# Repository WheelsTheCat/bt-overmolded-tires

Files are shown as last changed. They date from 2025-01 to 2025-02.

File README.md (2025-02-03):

# Box Turtle Overmolded Tires
# Thank you to Transmutated in the Box Turtle Discord for the excellent writeup and pictures!

Discussion here: [Discord Box Turtle Discussion](https://discord.com/channels/1229586267671629945/1315355814512562242 "Discord Box Turtle discussion").

## Tools
* hot glue gun
* hobby knife
* small pliers
* diagonal cutting pliers or something else strong enough to cut the "ice-cube tray"
* fine-tipped screwdriver or similar prying device

## Materials
* two-part rubber silicone; 10a, 15a and 20a will work.

## STL Files To Print
You can print these in whatever sacrificial filament you want to use as most of these parts won't be reusable. 
## The exception is the new-style wheels. Print these in whatever filament you are printing all of your accent color parts in to match your box turtle build.

Print settings:
- 0.2mm layer height.
- The Spiral Insert should be printed in vase mode and using the arachne wall generator. 
(Quality, Wall Generator, Arachne). Thanks Robnex!

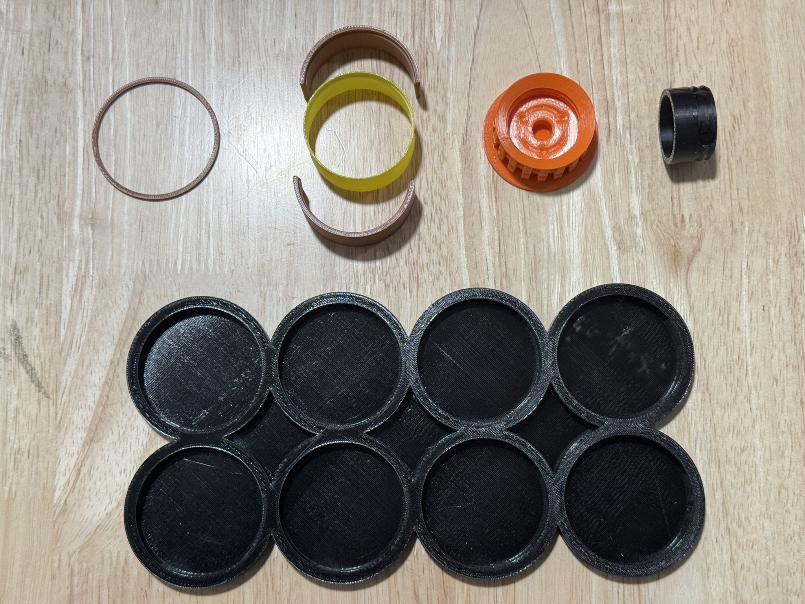
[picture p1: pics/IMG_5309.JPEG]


* 1 x [Ice Cube Tray](https://github.com/WheelsTheCat/bt-overmolded-tires/blob/main/stls/Ice%20Cube%20Tray.stl) - second row, position 1 in black
* 8 x [Retainers](https://github.com/WheelsTheCat/bt-overmolded-tires/blob/main/stls/Retainer.stl) - first row, position 1 in brown
* 8 x [Part 1](https://github.com/WheelsTheCat/bt-overmolded-tires/blob/main/stls/Part%201.stl) - first row, position 2, above yellow spiral insert
* 8 x [Part 2](https://github.com/WheelsTheCat/bt-overmolded-tires/blob/main/stls/Part%202.stl) - first row, position 2, below yellow spiral insert
* 8 x [Spiral Inserts](https://github.com/WheelsTheCat/bt-overmolded-tires/blob/main/stls/Spiral%20Insert.stl) first row, position two, in yellow
* 8 x [New Style Wheels](https://github.com/WheelsTheCat/bt-overmolded-tires/blob/main/stls/New%20Style%20Wheel.stl) first row, position 3, in orange
* 8 x [New Style Wheel Plugs](https://github.com/WheelsTheCat/bt-overmolded-tires/blob/main/stls/New%20Style%20Wheel%20Plug.stl) first row, position 4, in black

## Step 1
Assemble the spiral inserts combined with the retainer and parts 1 & 2. Observe that there is a lip that must be aligned for both parts and the spiral inserts. Once assembled, slide the retainer clip over the parts to keep them fastened. We'll call this the mold shell.

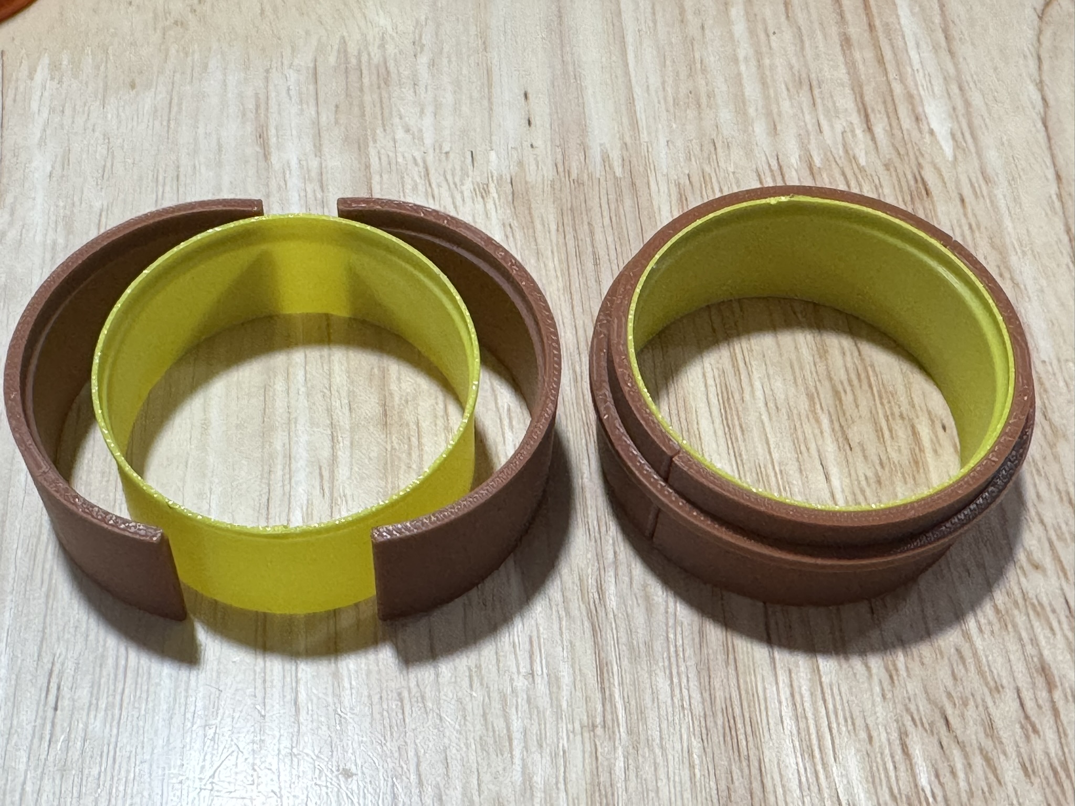
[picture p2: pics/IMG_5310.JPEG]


## Step 2
Attach the plug to the new-style wheel as pictured. Be sure the plug contacts the bottom of the wheel base.

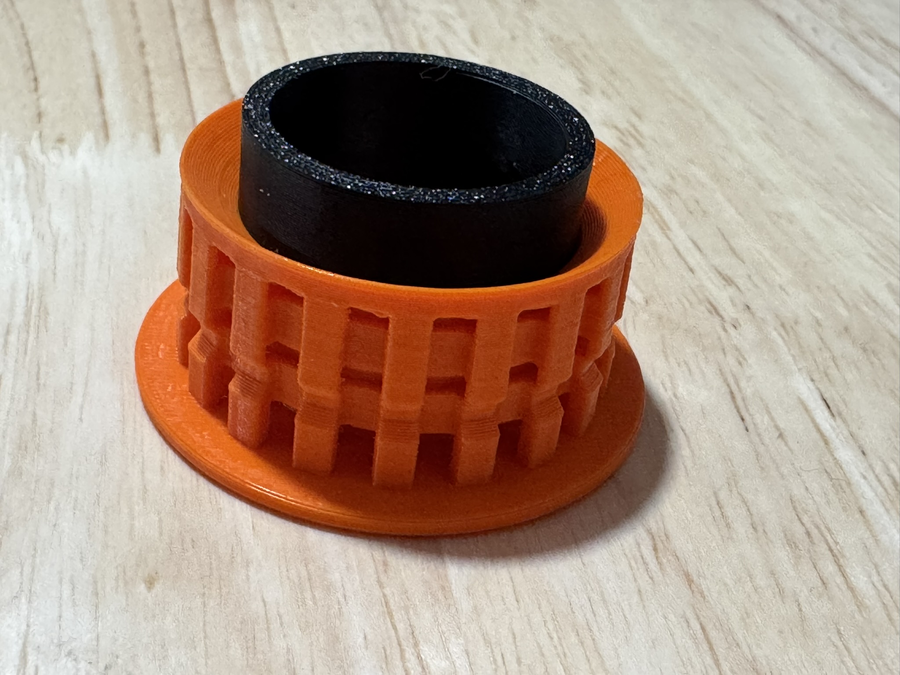
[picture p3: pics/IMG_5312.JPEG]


## Step 3
Place the assembled wheel base into each of the ice cube tray slots and then place the assembled mold shell on top of the wheel as shown. Using your hot glue gun, place a generous amount of hot glue around the base of the shell and the ice cube tray. This will ensure the poured rubber silicone won't leak much.

For sections between two wheels where it may be difficult to use the hot glue gun, you can apply a bit of hot glue to the side of the shell 5mm above the bottom. When you place the shell in the tray, it'll properly seal that section.

I found it easiest to work on two at a time instead of doing them all at once.

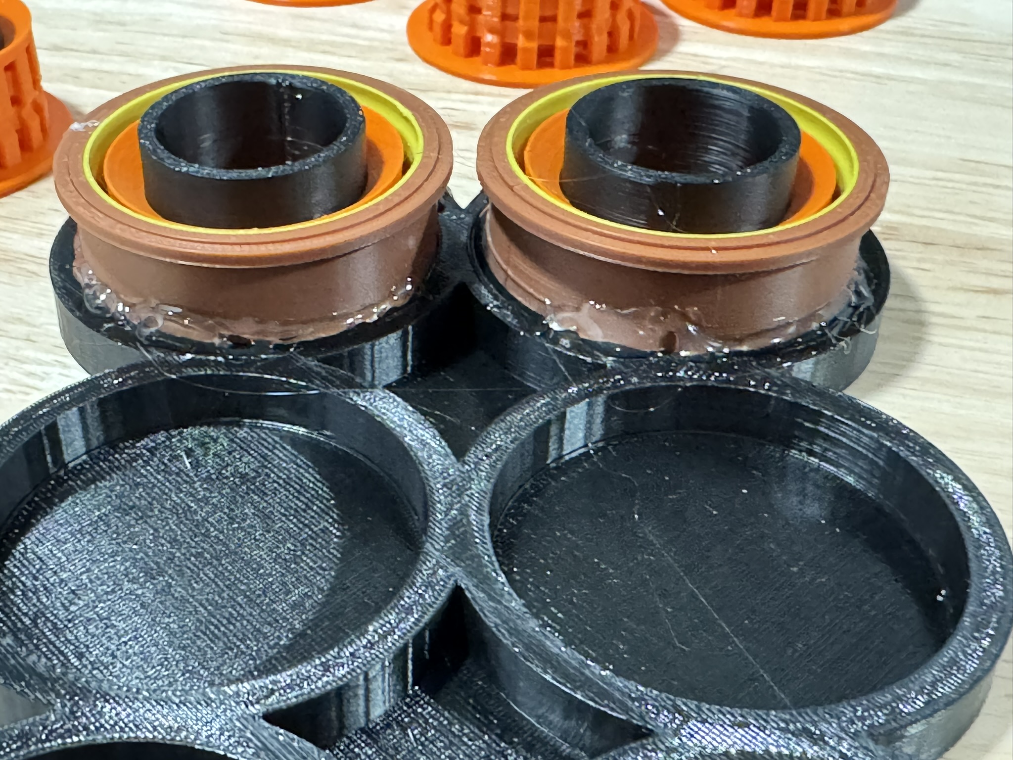
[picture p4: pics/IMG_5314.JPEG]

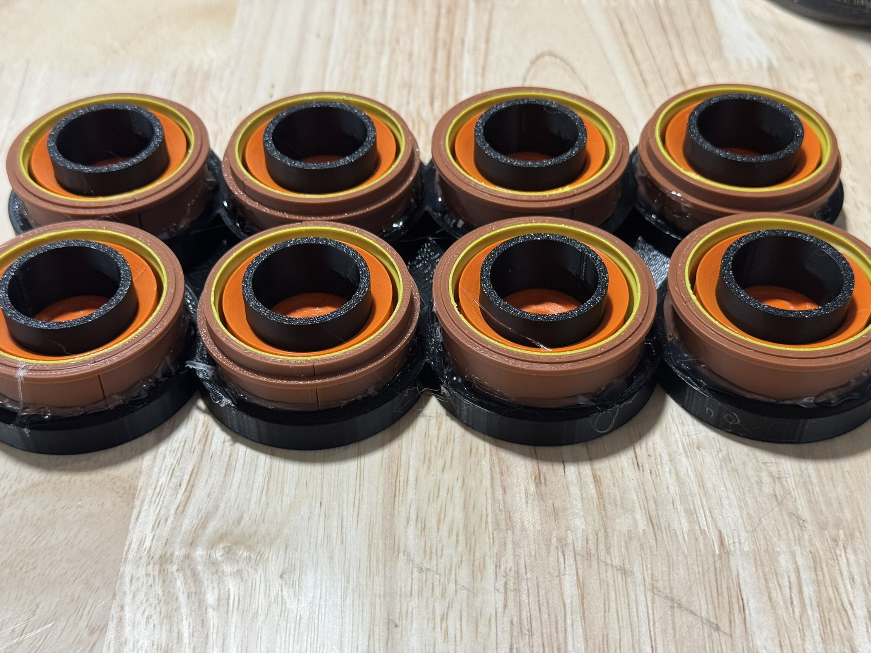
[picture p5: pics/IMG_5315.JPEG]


## Step 4
Now it's time to pour the material into the mold. Mix your material as instructed. Mixing a combined total of 150-160g of material should be sufficient. If you would like to color your rubber silicone, you can use mica powder. For reference, I used black and mixed 160g of material and used 5g of mica powder, and that was a rich black.

Fill to the brim of the shell. Don't worry if some material goes into the well where the plug is while moving between wheels; it'll seep in anyway but is easy to clean out when dry. Avoid it, but don't panic or try to clean it when wet.

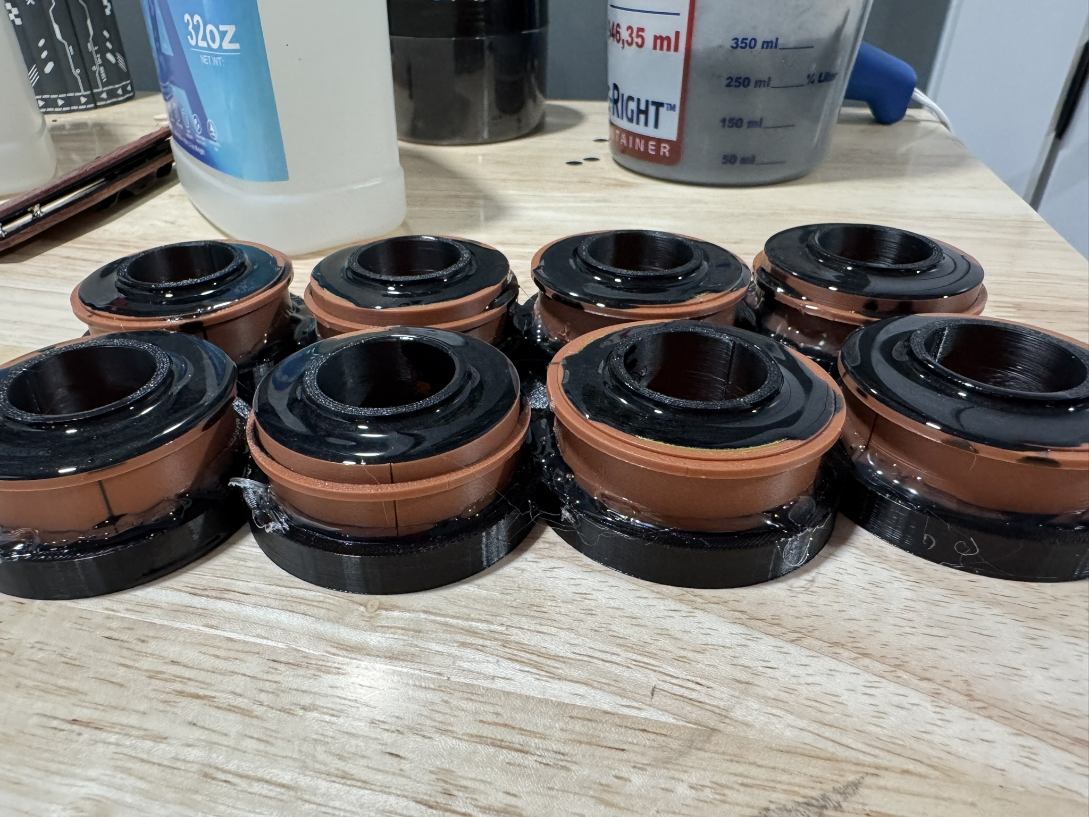
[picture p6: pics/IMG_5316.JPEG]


## Step 5
Break the molds! The ice cube tray is entirely sacrificial. I used diagonal clippers to effectively compromise the rings. From there, I used a pair of pliers to further create separation. I also found it useful to break the ice cube tray in half. This part of the write-up is use whatever means necessary to free the parts really.

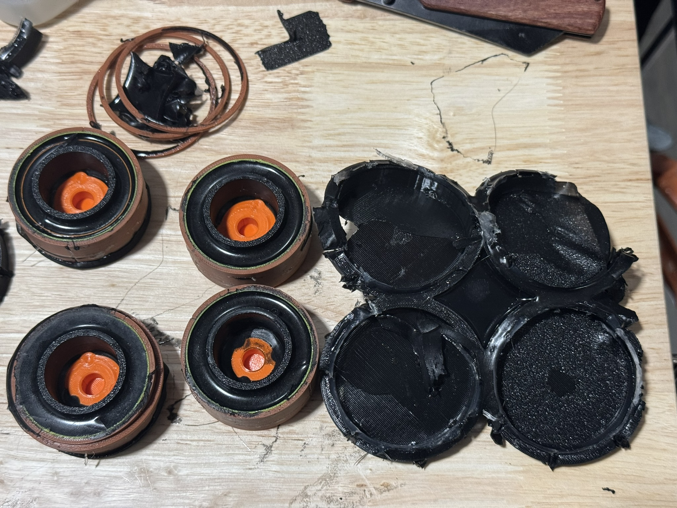
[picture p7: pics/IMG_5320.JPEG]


Once the parts are free of the ice cube tray, use something small to wedge between parts 1 or 2 and the spiral inserts. This shouldn't take much pressure, but I was careful as I didn't want to damage the molded parts.

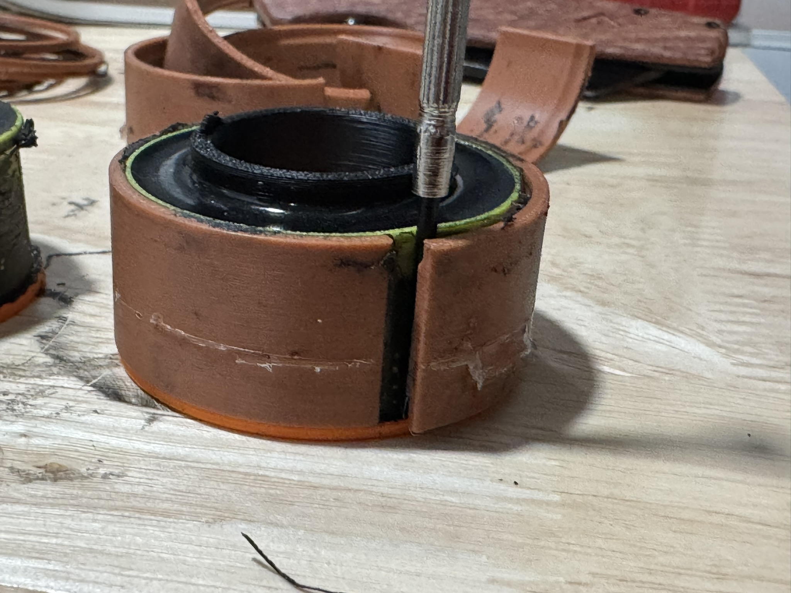
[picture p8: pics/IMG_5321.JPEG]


I didn't take a picture since it required two hands to do it, but you can use a hobby knife to score the spiral inserts and then remove them from the molded part.

Next, you'll use a pair of pliers and grab the plug. With your other hand, simply grab the base of the wheel and turn it until the plug is fully removed unthreaded from the wheel.

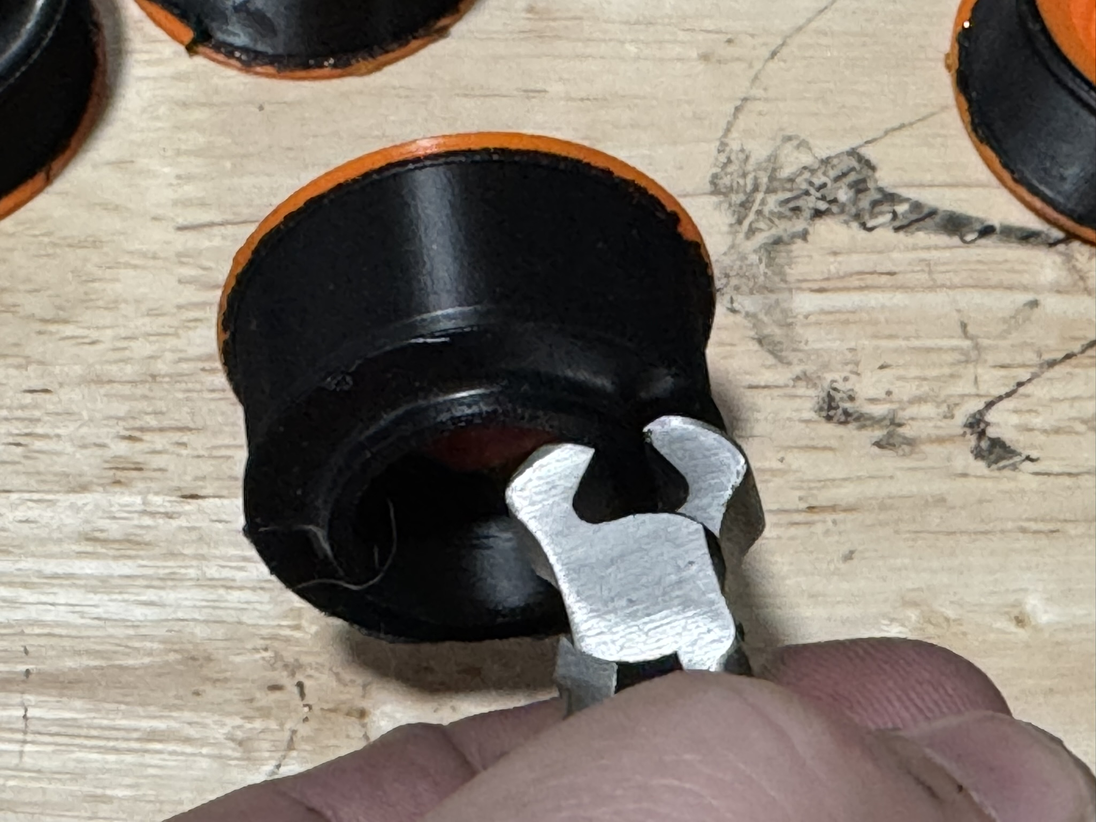
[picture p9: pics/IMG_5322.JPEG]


## Step 6
At this stage, you should have removed all mold shells and plugs and be left with a hopefully good-looking wheel. I spent a few minutes on each wheel with my hobby knife to lightly trim the excess material that got out between my shell and the wheel. Once scored, it was easy to remove the material. May not have even needed to use the knife, but I wanted to make sure it looked nice.

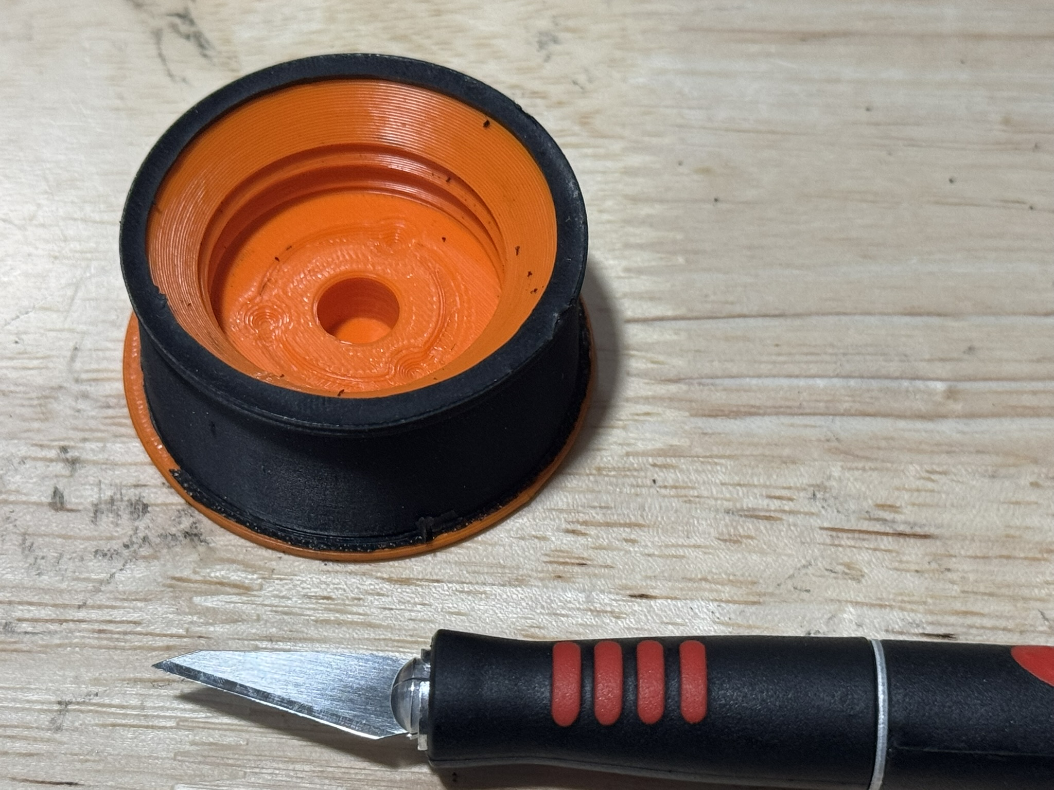
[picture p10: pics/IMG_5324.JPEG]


I didn't take a picture of it, but I had a good bit of rubber that was overlapping into the sloped area of the wheel. I cleaned this up with the hobby knife. Basically, I would jab the knife into the overlap and try to angle it between the outer wall of the wheel and basically went around the wheel with the knife. You end up with rubber donuts. The rubber pulls from the edge pretty easily here on the top edge.

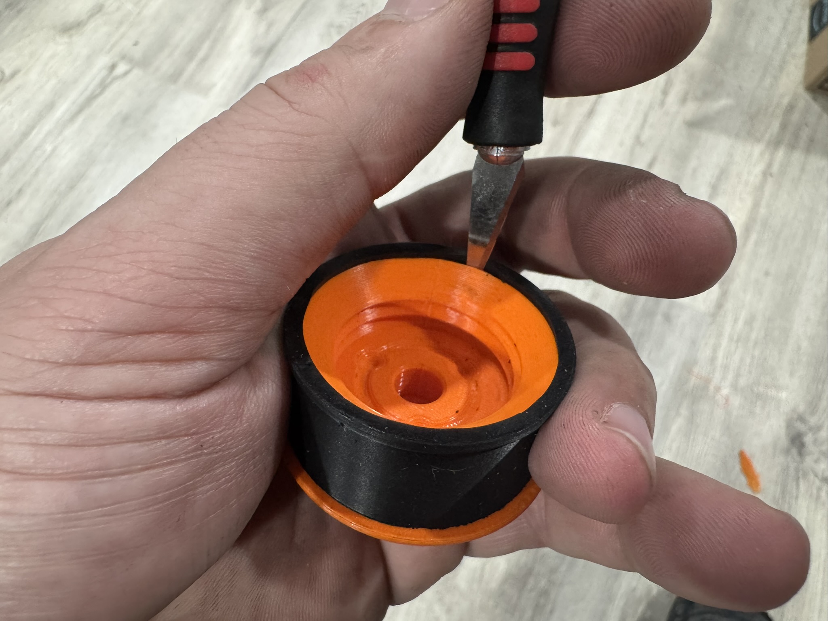
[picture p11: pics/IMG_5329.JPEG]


Here is what the donuts look like after you clean the excess out of the area.

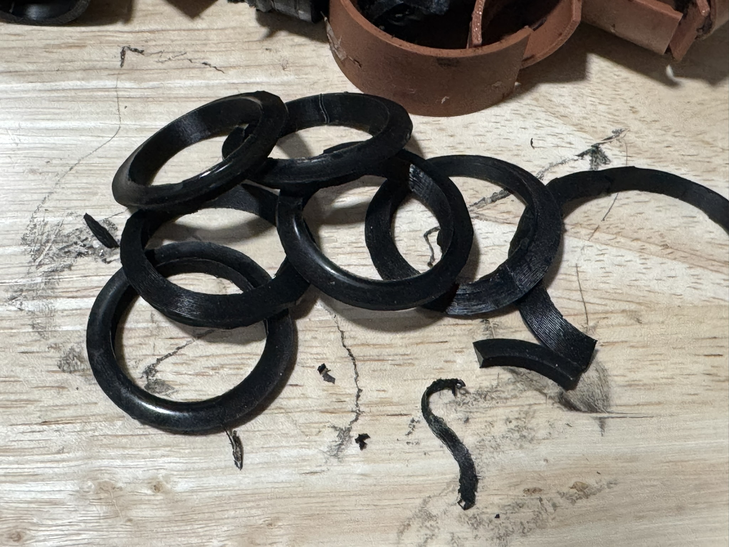
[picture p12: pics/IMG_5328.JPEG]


# End Results
My wheels came out very smooth and the 10a hardness rubber is extra soft and grippy. The mica powder I used had some glitter flakes, but that shouldn't impact anything. Looks really good and I'm sure this will be a bit nicer than the TPU. I can't say I'd change anything in the process at this point.

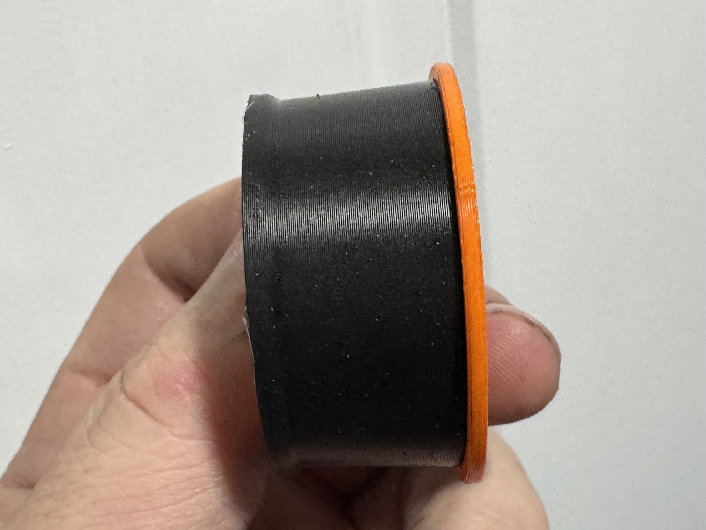
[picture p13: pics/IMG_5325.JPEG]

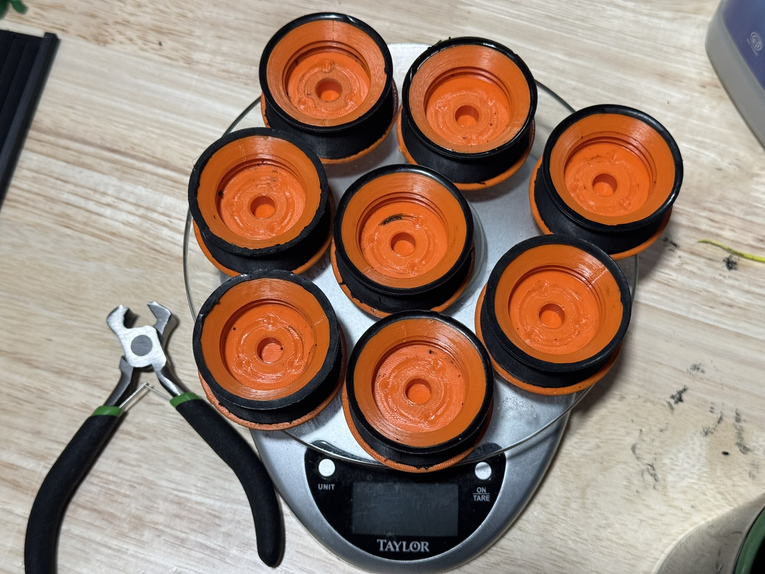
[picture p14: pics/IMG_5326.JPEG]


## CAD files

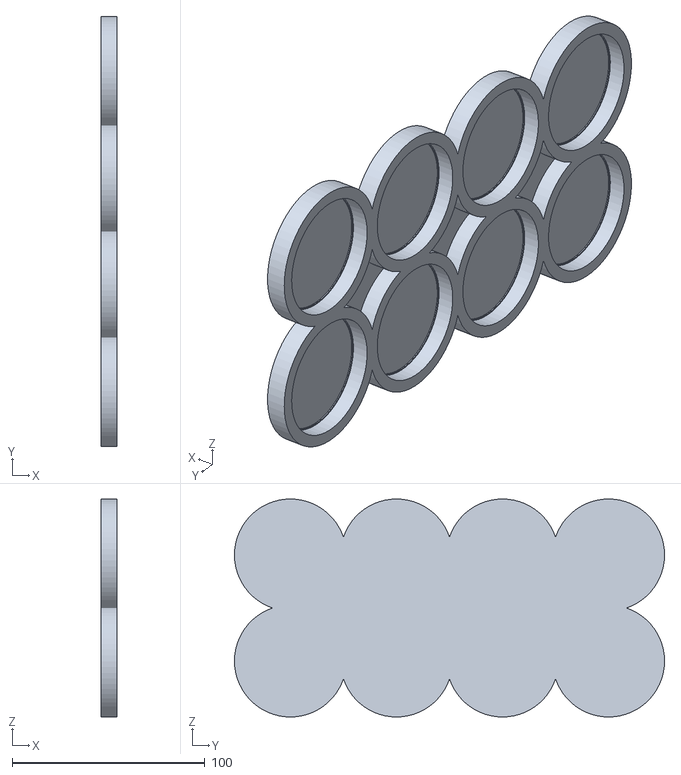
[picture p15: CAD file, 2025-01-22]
stls/Ice Cube Tray.stl
8.38 x 223.0 x 113.0

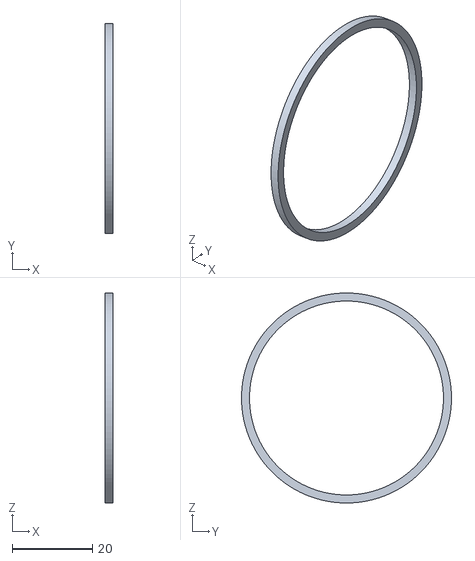
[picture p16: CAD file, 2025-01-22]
stls/Retainer.stl
2.00 x 52.2 x 52.2

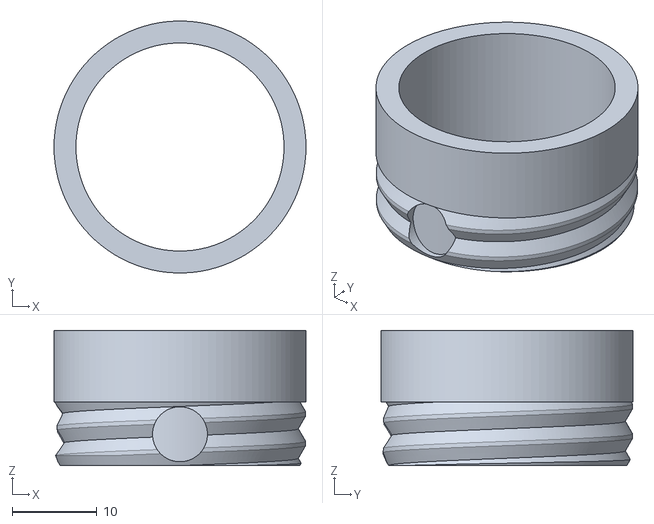
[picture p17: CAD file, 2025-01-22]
stls/New Style Wheel Plug.stl
29.8 x 29.8 x 16.0

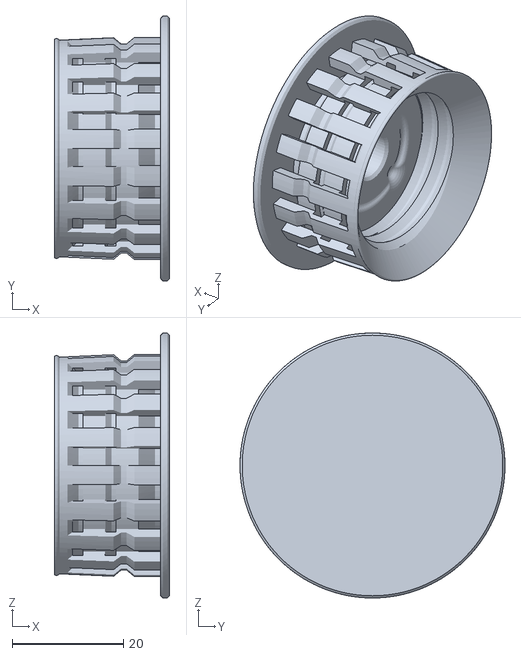
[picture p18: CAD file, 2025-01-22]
stls/New Style Wheel.stl
20.7 x 47.6 x 47.6

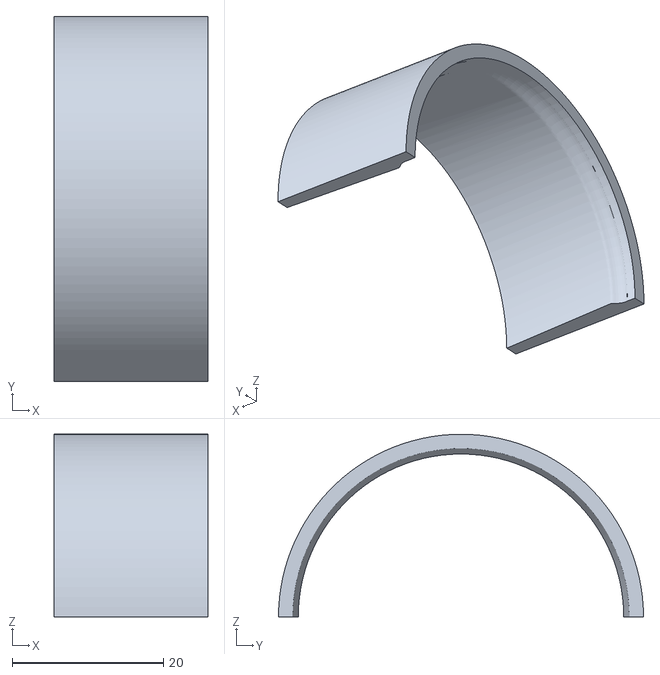
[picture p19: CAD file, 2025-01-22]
stls/Part 2.stl
20.3 x 48.2 x 24.1

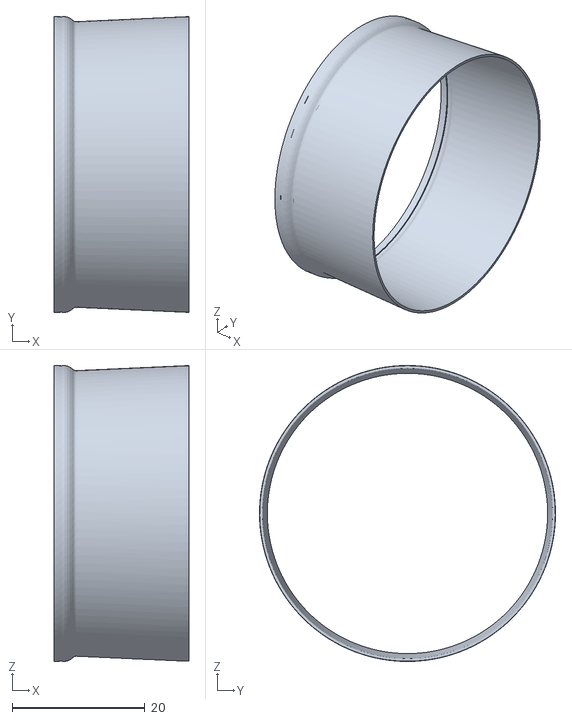
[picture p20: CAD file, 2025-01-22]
stls/Spiral Insert.stl
20.3 x 44.6 x 44.5

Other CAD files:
stls/Part 1.stl

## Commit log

2025-01-20 Update README.md with print settings
2025-01-22 Fixed Stls
    [Ice Cube Tray.stl, New Style Wheel Plug.stl, New Style Wheel.stl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]
